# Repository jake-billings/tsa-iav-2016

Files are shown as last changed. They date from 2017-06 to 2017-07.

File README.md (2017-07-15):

# tsa-iav-2016



This repository contains the work completed for the Technology Student Association (TSA) Integrated Autonomous Vehicle (IAV) competition for my team in 2016. The competition consisted of having a robot complete a course. Points were awarded for speed and completion of additional challenges. Points were subtracted for cost.

## Using my Work ##
Given that IAV is still an active competition, I figured it would be a good idea to add a guide here for using my work. I have an MIT license on this repository, so that means you're free to use it as long as you include that license and link back to me. That being said, if you are an IAV competitor, please make sure you abide by all TSA guidelines when working on your project. That means you can't use any of my designs or code for competition. Although, it's probably fine if you use them as a guide.

If this repository helped you, please cite it using my name, a link, and the DOI number from the top of this page. Also, feel free to send me an email letting me know it helped. [jake@jakebillings.com](mailto:jake@jakebillings.com).

Thanks so much.

## Hardware
The software relies on custom hardware developed using the Arduino Uno platform and standalone ATmega328. See the docs folder for custom hardware designs and the `/docs` folder. Electrical designs are in the `/hardware` folder.

### Bill of Materials (BOM)
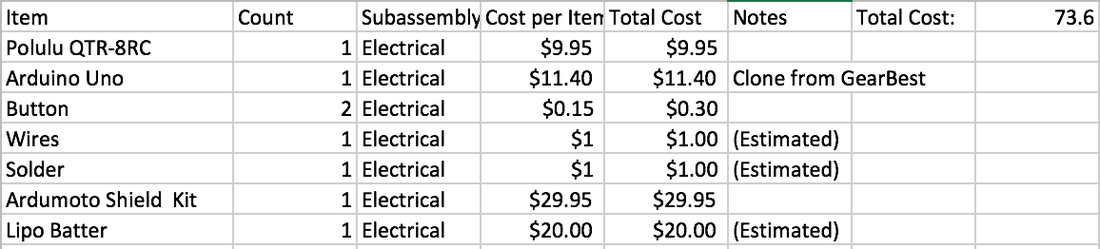
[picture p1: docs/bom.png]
BOM


[Click Here to Download BOM](docs/BOM.csv)

### Score over Time

In the TSA IAV competition, one of the largest contributing factors to score is time.

While this is pretty straight-forward, the effect of time on the Integrated Autonomous Vehicle (IAV) cannot be overlooked. The score decreases over time in a linear fashion. This shapes decisions made about the IAV because it must complete the course quickly in order to receive more points.

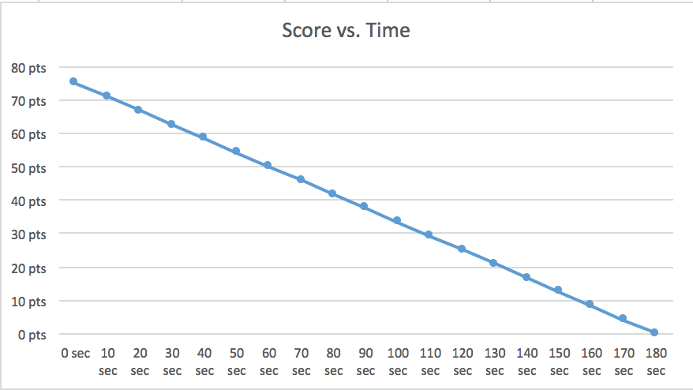
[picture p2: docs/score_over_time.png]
score_over_time


## Software
The software for the integrated autonomous vehicle is written using the Arduino platform. See the software folder in this repository for more. 

### Architecture

The Integrated Autonomous Vehicle utilizes multiple distinct programming layers allowing for abstraction, organization, and reusability. The final IAV code runs on top of line following and remote control receiver components that are non-specific to the specific task. These components were built on a low-level output hardware abstraction layer (HAL) insulates line following and remote control code from the underlying hardware specifics. PID is also abstracted into its own low-level component in order to allow for reusability. Low-level components and libraries run on top of the Arduino software platform, which runs on top of the ATMEGA328 process.

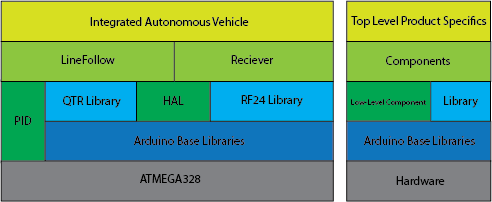
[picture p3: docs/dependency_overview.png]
dependency_overview


### Scheduling

Special care is taken to ensure that the PID loop runs at a precise interval of 10ms. This matters because it is impossible to tune the derivative component accurately if the time between error measurements is inconsistent. This is not an issue for a program where the main loop contains only a PID loop; however, the program also contains code to read from the radio receiver and to process commands. As a result, special care is taken to ensure consistent execution of the control loop.

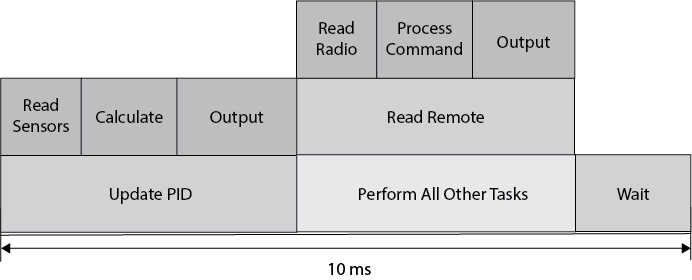
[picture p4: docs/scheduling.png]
scheduling


### Control Theory

The line following algorithm utilizes a piece of control theory known as Proportional-Integral-Derivative (PID) control. The integral piece is not used in this application, so it is sometimes referred to as just PD control. The right describes the control loop in block-diagram form. Measured displacement from being centered on the line is used to calculate a difference in motor power between left and right motors. This is added to the initial speed for one motor and subtracted from the other in order to rotate the vehicle such that it veers back onto the line.

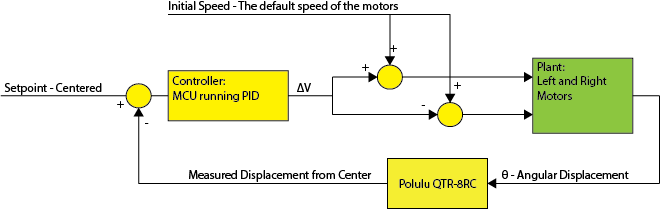
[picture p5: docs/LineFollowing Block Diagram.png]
Line following block diagram


### System Flow Chart

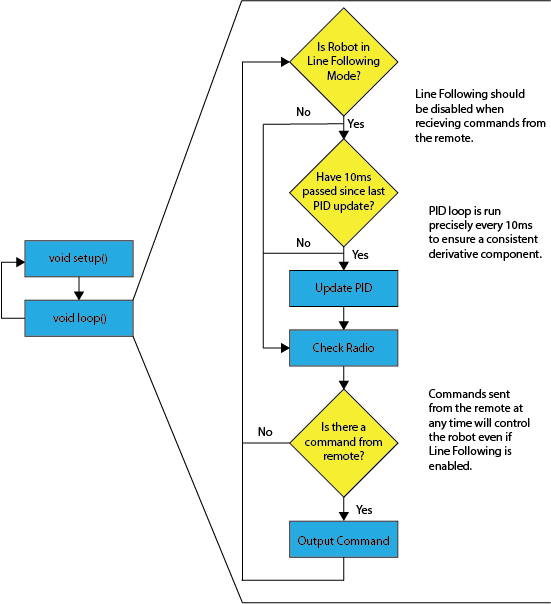
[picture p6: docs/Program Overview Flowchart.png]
program overview


## Mechanical

### Payload Retrieval Subassembly
This plan, designed for manufacturing using a laser engraver, is the first prototype of Version 1 of Concept 1 for Subassembly 1, the payload retrieval assembly. The large discs, subassemblies a1 and b1, are designed to be glued inside the edges of a 3" schedule 80 PVC pipe in order to allow for a servo and an axle to attach to the scoop. The axle pieces are designed to be glued together vertically to form a 0.5 in. diameter cylinder to form an axle to run from subassembly b1 to support 2. Supports 1a and 1b are designed to hold a RadioShack 2730766 servo. The horn of that servo shall be glued and screwed to subassembly a1. The screw hold tests exist to allow testing of various dimensions of screw holds in case the once centered in subassembly a1 is incorrectly sized. Support joint tests exist to test the dimensions of the sockets that the feet of the supports will be glued into on the main chassis. A 1x1 inch box is included to ensure proper scale throughout the manufacturing process.

#### Drawing
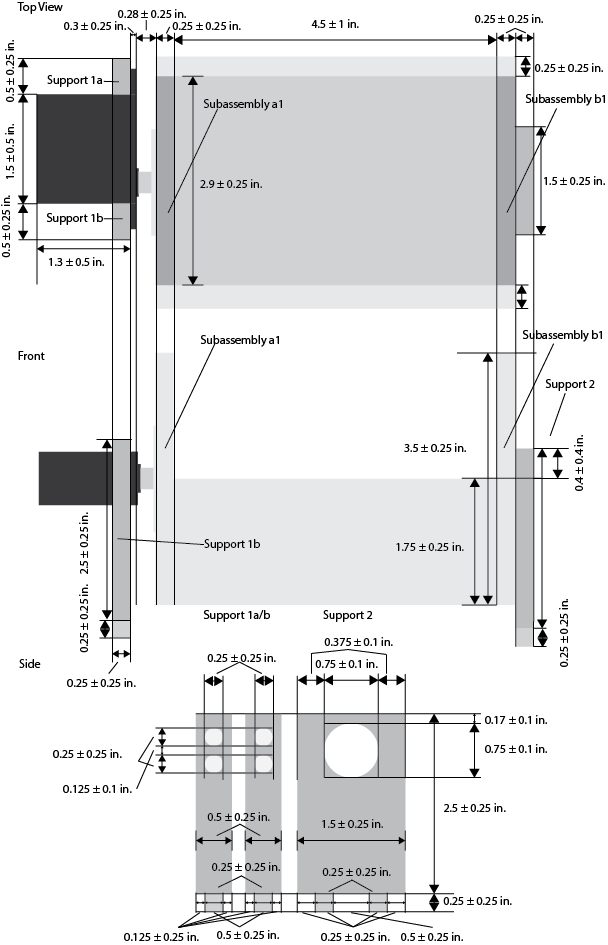
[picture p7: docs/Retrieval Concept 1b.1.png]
Payload Retrieval Subassembly


#### Laser engraver cutting plans
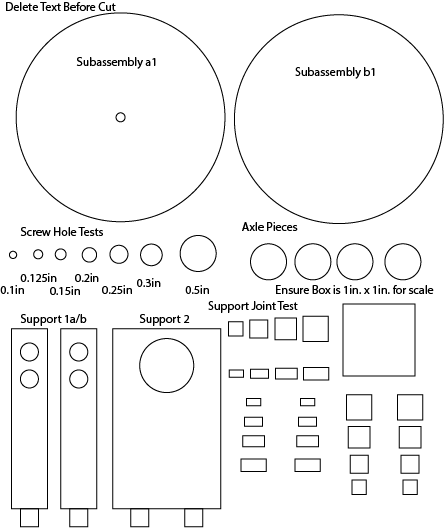
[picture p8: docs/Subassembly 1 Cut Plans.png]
Payload Retrieval Subassembly


### Chasis
The chasis is the main mechanical component of the IAV. It consists of the motors and 

#### Prototype (Version 1)
Early prototypes that tested line following and remote control functionality utilized the SparkFun RedBot chassis. This allowed electronics to be easily attached to the chassis and for new concepts to be tested before designing and building a final chassis. The SparkFun RedBot was used in Version 1 of the robot with Version 1 of the Source Code in the run-off competition December 4th, 2015

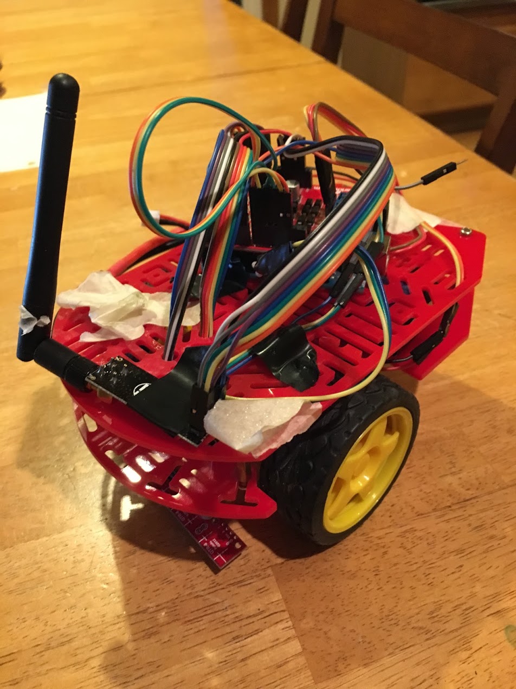
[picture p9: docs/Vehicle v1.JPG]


#### Version 2
The second version of the IAV chassis solves all of the above problems with the first generation chassis. The design can be manufactured utilizing a laser engraver and any material strong enough to support the weight of the vehicle. It could in theory be manufactured using acrylic plastic, aluminum, or cardboard. This gives flexibility to fix the cost issue. The second generation chassis will ride fairly close to the ground. It is low enough to allow for the payload retrieval subassembly to capture a tennis ball from the pedestal while sitting on top. It does this by mounting wheels above the main chassis itself and effectively hanging from the center of the wheels.
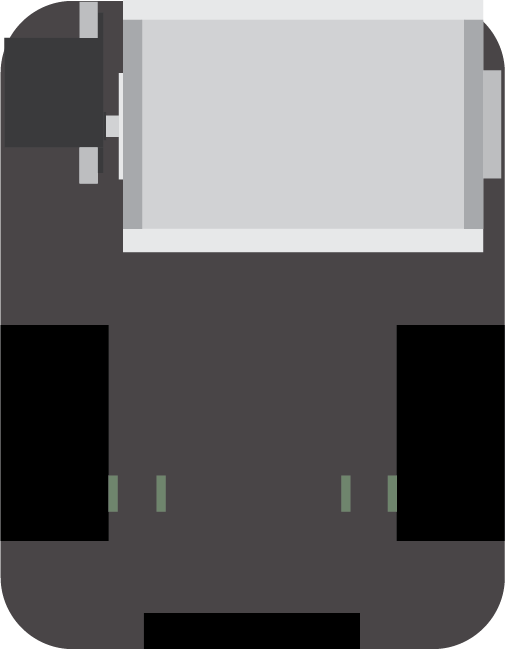
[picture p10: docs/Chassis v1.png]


Wheel bays are cut from the left and right of the vehicle. A front section is cut to allow for the line following sensor to be installed. Mounts for the motors and wheels are cut as small rectangles near the wheel bays. The top contains circular screw holes for a ball bearing to serve as a rear wheel, and rectangles are cut to mount the payload retrieval subassembly. This early revision contains an error in the sensor mount that cuts the screw holes for the sensor mount out of the chassis.

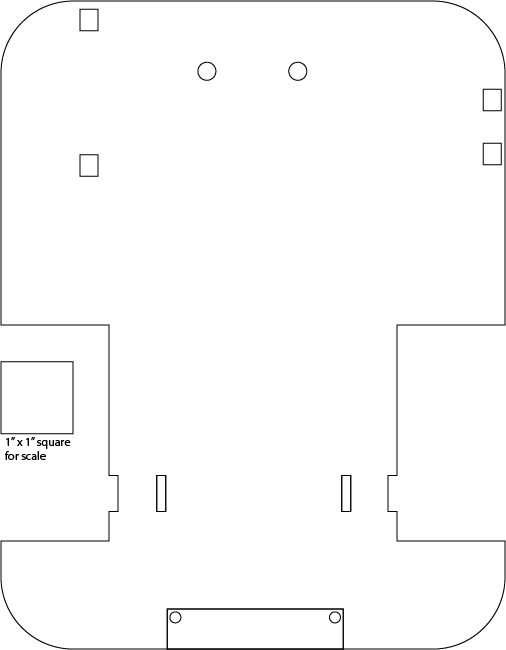
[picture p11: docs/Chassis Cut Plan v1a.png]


### Practice Courses

Early iterations of the IAV were tested on a track built exclusively to test line following. The course was far more portable and far smaller the the actual practice course. This course was primarily used to test early prototypes of a line following vehicle leading up to the December 4th, 2015 run offs.

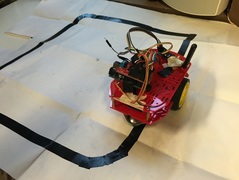
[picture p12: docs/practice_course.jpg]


A detailed replica of the the final course as detailed in the COTSA Call to Conference 2016 was created in order to test the vehicle. A replica was designed to use entirely 3/4" electrical tape on a large sheet of paper in order to provide accurate dimensions for line following as well as portability. The course can be rolled up in order to allow for easy transportation.

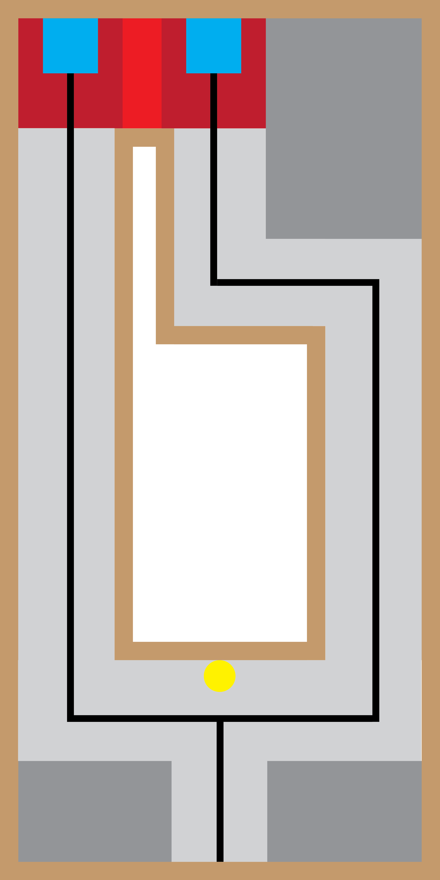
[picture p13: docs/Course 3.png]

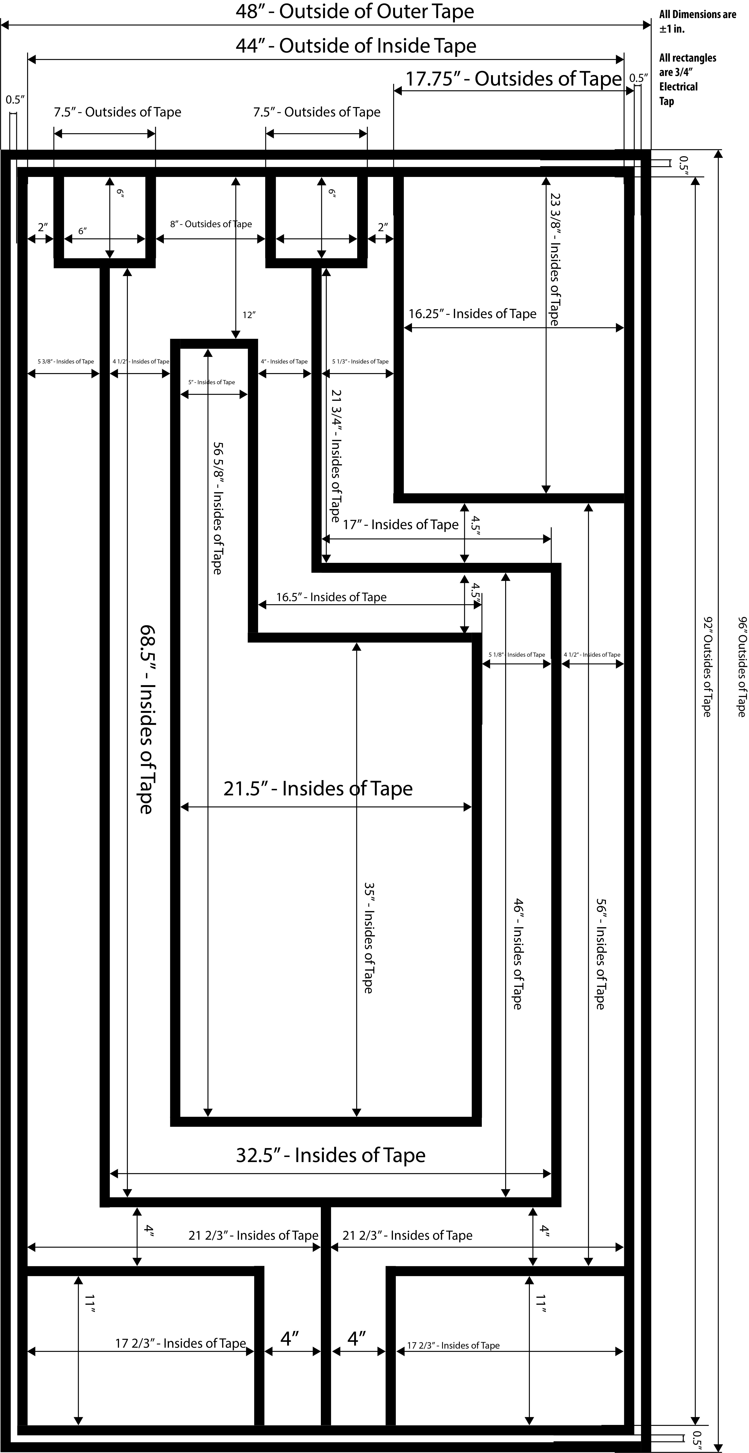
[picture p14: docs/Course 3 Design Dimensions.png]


## Summary
Early prototypes that tested line following and remote control functionality utilized the SparkFun RedBot chassis. This allowed electronics to be easily attached to the chassis and for new concepts to be tested before designing and building a final chassis. The SparkFun RedBot was used in Version 1 of the robot with Version 1 of the Source Code in the run-off competition December 4th, 2015. A school chassis was used; however it carried some major issues.
The Chassis Retailed at over $35.00. This is unacceptable in the final design.
The Chassis was too high off of the ground to successfully collect the payload.
The line following sensor was only able to be attached utilizing a single screw in addition to hot glue.
The second version of the IAV chassis solves all of the above problems with the first generation chassis. The design can be manufactured utilizing a laser engraver and any material strong enough to support the weight of the vehicle. It could in theory be manufactured using acrylic plastic, aluminum, or cardboard. This gives flexibility to fix the cost issue. The second generation chassis will ride fairly close to the ground. It is low enough to allow for the payload retrieval subassembly to capture a tennis ball from the pedestal while sitting on top. It does this by mounting wheels above the main chassis itself and effectively hanging from the center of the wheels.
A laser cut plan was used for the second generation chassis. Wheel bays are cut from the left and right of the vehicle. A front section is cut to allow for the line following sensor to be installed. Mounts for the motors and wheels are cut as small rectangles near the wheel bays. The top contains circular screw holes for a ball bearing to serve as a rear wheel, and rectangles are cut to mount the payload retrieval subassembly. This early revision contains an error in the sensor mount that cuts the screw holes for the sensor mount out of the chassis.
The Integrated Autonomous Vehicle utilizes multiple distinct programming layers allowing for abstraction, organization, and reusability. The final IAV code runs on top of line following and remote control receiver components that are non-specific to the specific task. These components were built on a low-level output hardware abstraction layer (HAL) insulates line following and remote control code from the underlying hardware specifics. PID is also abstracted into its own low-level component in order to allow for reusability. Low-level components and libraries run on top of the Arduino software platform, which runs on top of the ATMEGA328 process.
Special care is taken to ensure that the PID loop runs at a precise interval of 10ms. This matters because it is impossible to tune the derivative component accurately if the time between error measurements is inconsistent. This is not an issue for a program where the main loop contains only a PID loop; however, the program also contains code to read from the radio receiver and to process commands. As a result, special care is taken to ensure consistent execution of the control loop.
The line following algorithm utilizes a piece of control theory known as Proportional-Integral-Derivative (PID) control. The integral piece is not used in this application, so it is sometimes referred to as just PD control. The right describes the control loop in block-diagram form. Measured displacement from being centered on the line is used to calculate a difference in motor power between left and right motors. This is added to the initial speed for one motor and subtracted from the other in order to rotate the vehicle such that it veers back onto the line.

### Other Projects ###
Checkout my other projects at [http://www.jakebillings.com](http://www.jakebillings.com) or contact me via [LinkedIn](https://www.linkedin.com/in/jake-billings/).

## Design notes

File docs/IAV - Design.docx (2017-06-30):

IAV - Design

Roles

- Lead: Jake Billings
- Support: Erast Davidjuk
- Support: Jeremy Goldman

Features

Complete

In Progress

Blocked

Major Issue

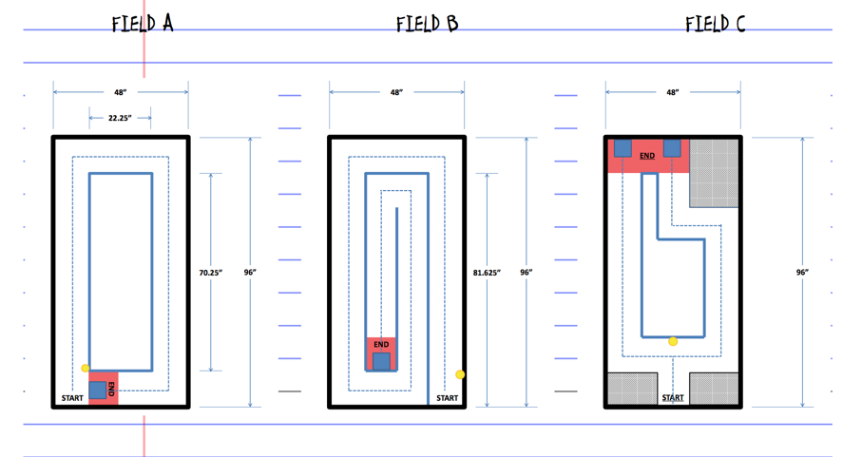
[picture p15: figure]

Practice Board Member(s): Erast, hopefully other team Status: In progress | Recreate field C from the COTSA document At least to start, create a 2D version of the board using a large paper or cloth and electrical tape. The dimensions and tracking line must be accurate, and field features must be labeled. | THIS NEEDS TO GET DONE
Initial RedBot Status: Ready | Control RedBot chassis using Arduino Uno. - Move forward - Move backward - Rotate 360 degrees clockwise and counterclockwise
Line following Status: Awaiting parts and practice board | Create line following algorithm using - Arduino Uno/Sparkfun RedBot - Redbot Chassis - Pololu sensor array - PD Control
NRF24L01 Communication Status: Completed by Jake | Establish Serial communication between two Arduino Unos utilizing the NRF24L01 boards. - Must be able to send commands for motors for future manual control
Manual Control Member(s): Jake | Establish a method of control for the IAV utilizing communication through NRF24L01. - The speed of both motors must be controlled in order to allow for steering of the robot. - Commands will be sent via NRF24L01 | Waiting on new Joy Sticks; Otherwise complete

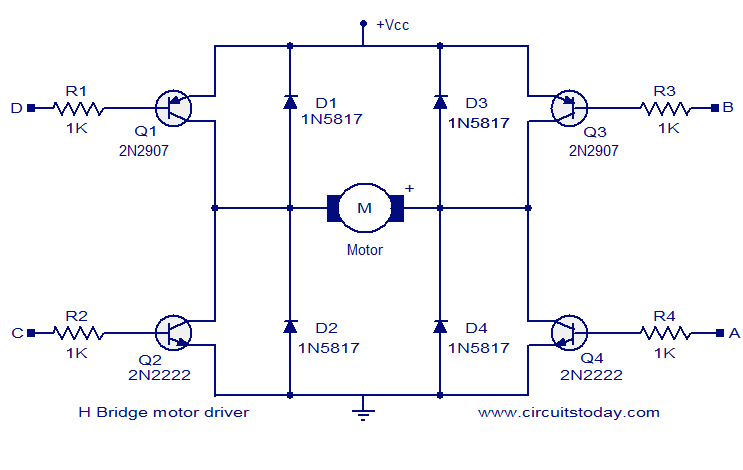
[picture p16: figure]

Create H-Bridge from transistors Assigned: Jeremy Goldman | Create an H-Bridge to go on top of the Arduino/ATMega controller https://123d.circuits.io/circuits/1089194-h-bridge-try-1 | Breadboard version complete.
Chassis Redesign/Payload retrieval method Member(s): All, Jake Status: | - Chassis must be redesigned using cheap/free materials. - New chassis will be capable of acquiring payload. - Draft drawings will be sketched - CAD will be completed
Build Chassis and Redesign Members: All, Jake | - Build the designed chassis and make improvements as necessary - Test, Test, Test - Document! | Waiting on laser engraving
Develop Autonomous Program Member(s): Jake Status: | - Abstract PID - Abstract Line following - Abstract Receiver - Create central program - Positioning - Color-based? - Vehicle will be able to complete course autonomously and as quickly as possible - Vehicle will be able to retrieve payload and deliver it to target at the end of the course. - Document | Waiting on Chassis prototype and practice mat

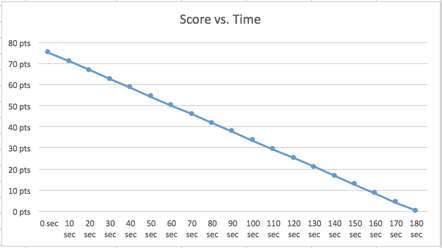
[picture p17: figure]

Increase Speed and Optimize Member(s): All, Jake | - The score decreases over time, so our vehicle has to be the fastest DOCUMENT! | Waiting on Develop Autonomous Program
Run blink on ATMEGA328 Member(s): Jeremy | - Run blink off of an ATMEGA (use a multimeter instead of LED) | Done.
Build custom boards Member(s): Jake/Jeremy Status: | - Flash the 328 using an Uno, and connect to the robot. Everything should function nominally for a fraction of the price. - Solder circuit onto perfboard

Documentation

Member(s): All, Jeremy, Jake

Status: Waiting on more info

B. Every team shall submit a standard three ring 8.5” x 11” engineering binder which captures the design process. The notebook shall contain:

- A title page with the event title, state conference information, including date of the conference and the team ID number.
- Minimum two (2) page typewritten description of the vehicle including the building system/components used. This description should include a brief discussion of the design problem, the engineering design process, and the final solution. Include a discussion of any data, calculations, and iterations taken during the design process.
- Bill of Materials (BOM) / Budget: A complete list of all parts, materials, and components used on the vehicle. Additional bonuses will be awarded to teams that use readily available materials and low-cost solutions.
- Data Tables and Calculations: Tables of original experimental data illustrating the iterations, trials and calculations should be included and properly documented with dates and times of the experiments.
- Complete mechanical engineering drawings of the vehicle shall be provided.

i. Drawings may be done by hand or using computer-aided design (CAD).

ii. The drawings should include at a minimum an orthographic or isometric sketch and three section views illustrating the front, top and side profiles of the vehicle with appropriate geometric dimensioning and tolerancing.

- Schematic drawings of the wiring, power system and sensors shall be provided.
- Use color coding and labels on your schematic where appropriate.
- Pseudo-code / algorithm. Contestants should include a flow chart, diagram or illustration of their program and program flow.
- Print-out of the complete source code of the program shall be included. Your program should be well documented and commented to allow judges to interpret your algorithm and program flow.

Work Log

Date | Time | Member(s) | Work
09/12/2015 | 65 Minutes | Jake Billings | - Design document created - Sensors and microcontrollers researched - Concept plans drawn - Rough plan of work including main features created
10/01/2015 | 100 minutes | Jeremy Goldman, Erast Davidjuk, and Jake Billings | - Begin assembly of practice track
10/06/2015 | 100 minutes | Jeremy Goldman, Erast Davidjuk, and Jake Billings | - Planning - Code review - H-Bridge research
Next | | | Remote controlled redbot with ardumoto WORKING

Bill of Materials (Working Copy and Log)

Put all purchased and used materials on this log. This is not the final log, so do not delete anything. Do not include materials used to build practice tracks.

Material | Purpose | Current Use/Status | Price and Source
Pololu QTR-8RC Reflectance Sensor Array (Line following sensor) | Used to determine the vehicle’s position relative to the tracking line. | Attached | $9.95 https://www.pololu.com/product/961
Arduino Breadboard Basic Kit - ATMEGA328P-PU With Bootloader 16MHz Crystal G36 | Microcontroller | In main Non critical but could reduce price of robot | $7.49 http://www.ebay.com/itm/151744703049
NRF24L01 | Transmitter/Receiver | In use. | $3.99 http://www.ebay.com/itm/like/191542825497?ul_noapp=true&chn=ps&lpid=82
Ardumoto | Motor driver | In use. | $24.99 https://www.sparkfun.com/products/9815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
RedBot Chasis | Chasis | In use. | ~$15.00 (from school) https://www.sparkfun.com/products/retired/10825

Obsolete Planning

Possible Members

On Team

Tentative

Not on Team

Candidate

- Jake Billings - Lead
- Scott McIntyre - Support/Notebook
- Jeremy Goldman - Support/Notebook
- Erast Davidjuk - Support/Notebook
- Simone Ong - Support/Notebook
- Sebastian del Barco - Support
- Lauren Martin - Notebook

Jake Billings 09/12/2015 TSA

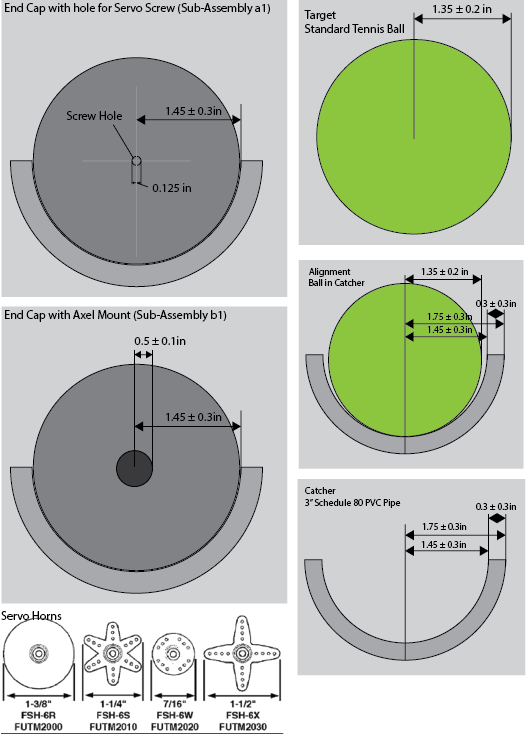
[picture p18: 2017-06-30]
docs/Retrieval Concept 1.png

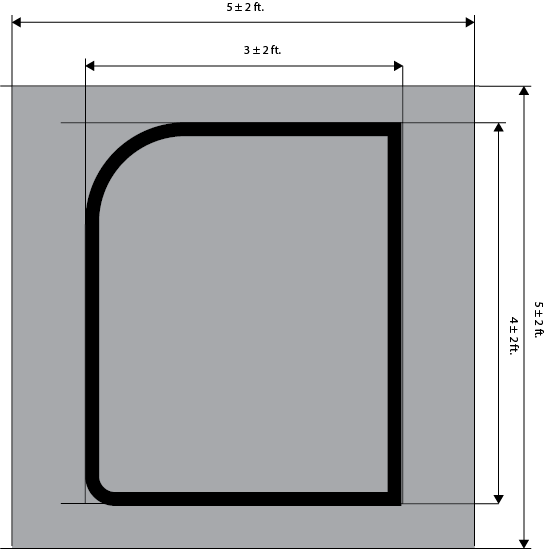
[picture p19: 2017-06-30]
docs/LineFollowing Course.png

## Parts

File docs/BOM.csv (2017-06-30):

Item | Count | Subassembly | Cost per Item | Total Cost | Notes | Total Cost: | 43.49
22nF Capacitor | 2 | Electrical | $0.04 | $0.08
16MHz Crytal Oscillator | 1 | Electrical | $0.50 | $0.50
PN2222 Transistor | 8 | Electrical | $0.03 | $0.24
Rectifier Diode | 8 | Electrical | $0.04 | $0.32
10 kOhm Resistor | 8 | Electrical | $0.04 | $0.32
Polulu QTR-8RC | 1 | Electrical | $9.95 | $9.95
NRF24L01 | 2 | Electrical | $1.99 | $3.98
ATMEGA328 | 2 | Electrical | $1.55 | $3.10
JoyStick | 2 | Electrical | $2.25 | $4.50
Button | 2 | Electrical | $0.15 | $0.30
Wires | 1 | Electrical | $1 | $1.00 | (Estimated)
Solder | 1 | Electrical | $1 | $1.00 | (Estimated)
Perfboard | 2 | Electrical | $8.95 | $17.90
Voltage Regulator | 1 | Electrical | $0.30 | $0.30

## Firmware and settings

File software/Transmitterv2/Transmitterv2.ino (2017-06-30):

#include <SPI.h>
#include "RF24.h"

#define COMMAND_SIZE 4

// Clockwise and counter-clockwise definitions.
// Depending on how you wired your motors, you may need to swap.
#define FORWARD  HIGH
#define BACKWARD LOW

// Motor definitions to make life easier:
#define MOTOR_A 0
#define MOTOR_B 1

RF24 radio(7, 8);
byte TRANSMITTER_ADDRESS[] = "EAKJB_RECEIVER";
byte RECEIVER_ADDRESS[] = "EAKJB_TRANSMITTER";

void setup() {
  //Initialize serial...
  Serial.begin(9600);
  Serial.print("Intializing transmitter...");

  //Initialize radio...
  radio.begin();

  //Set power level to low becaue communication is short-range
  radio.setPALevel(RF24_PA_LOW);

  //Open reading and writing pipes (addresses)
  //Switch the addresses on the transmitter
  radio.openWritingPipe(RECEIVER_ADDRESS);
  radio.openReadingPipe(1, TRANSMITTER_ADDRESS);

  //Start listening
  radio.startListening();

  //Notify debugger that initialization has finished.
  Serial.println("Done.");
}

void loop() {
  int reading = analogRead(A0);
  int reading2 = analogRead(A1);
  
//  Serial.println(reading);
//  Serial.print("Transmitting command...");
  
  byte val;
  byte dir;
  if (reading>=512) {
    val=map(reading,512,1023,0,257);
    dir=FORWARD;
  } else {
    val=map(reading,511,0,0,257);
    dir=BACKWARD;
  }
  byte val2;
  byte dir2;
  if (reading2>=512) {
    val2=map(reading2,512,1023,0,257);
    dir2=FORWARD;
  } else {
    val2=map(reading2,511,0,0,257);
    dir2=BACKWARD;
  }
  Serial.print(val);
  Serial.print('\t');
  Serial.println(val2);
  
  byte commandA[COMMAND_SIZE] = {0x02, MOTOR_A, val, dir};
  byte commandB[COMMAND_SIZE] = {0x02, MOTOR_B, val, dir};

  radio.stopListening();

  radio.write(&commandA, sizeof(byte)*COMMAND_SIZE);
  delay(80);
  radio.write(&commandB, sizeof(byte)*COMMAND_SIZE);

  radio.startListening();

//  Serial.println("Done.");

  delay(80);
}

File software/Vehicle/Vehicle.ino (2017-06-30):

#define DEBUG true
#define LINE_FOLLOW_STEP_INTERVAL 10 //Run line following loop every 10 milliseconds

void setup()
{
#if DEBUG
  Serial.begin(9600);
#endif

  lineFollowSetup();

  pinMode(7,INPUT);
  while (!digitalRead(7)) {
    //Wait
  }
}

//The last time in milliseconds from boot that the line following loop ran
long lastLineFollowStep = -1;
bool lineFollowEnabled = true;
void loop() {
  long mils = millis();

  if (lineFollowEnabled) {
    //Run the loop once every 10 milliseconds
    if ((mils - lastLineFollowStep) >= LINE_FOLLOW_STEP_INTERVAL) {

      //Run the loop
      lineFollowStep();

      //Store the time that the loop ran
      lastLineFollowStep = mils;
    }
  } else {
    halDrive(0, 0);
    halDrive(1, 0);
  }

#if DEBUG
  if (Serial.available()) {
    Serial.read();
    lineFollowEnabled = !lineFollowEnabled;
  }
#endif
}

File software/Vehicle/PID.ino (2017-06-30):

/**
 * Abstraction of PID math
 * 
 * Currently, only proportional and derivative math is implemented
 * No steady-state errors have been present yet, so the integral
 * componenet has not been implemented.
 * 
 * setpoint - The ideal condition of the system
 * sig - The input into the control loop (for instance, the QTR sensor reading)
 * lastSig - The input into the control loop in the last step (used to calculate derivative)
 * KP - weight of the proportional component of the error
 * KD - weight of the derivative component of the error
 */
int pid(int setpoint, int sig, int lastSig, float kp, float kd) {
  //Calculate error and last error from input signal and setpoint
  int error = sig - setpoint;
  int lastError = lastSig - setpoint;
  
  //Perform the pid calculation by applying KP and KD weights
  //to the error and the derivative of the error.
  int output = kp * error + kd * (error - lastError);

  return output;
}

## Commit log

2017-06-30 Add documentaion from original project in 2016
    [BOM.csv, BOM.xlsx, Scoring Over Time.xlsx]
2017-06-30 Add Frizing files that describe the hardware from the original project in 2016
    [TransmitterV1.fzz, TransmitterV2.fzz, Wiring Diagram v2.fzz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]
